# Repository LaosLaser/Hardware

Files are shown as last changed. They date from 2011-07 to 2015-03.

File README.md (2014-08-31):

Hardware
========

PCB Designs for the laos project (mainboard)
* 2 - Development version
* rev0.1 - small first series
* rev0.2 - used in various lasers
* rev0.3 - latest version
* rev0.4 - Nr of fixes. Introduced dagerous hardware errors: Grounds disconnected. See wiki!
* rev0.5 - Hardware fixes: routing and ground plane
* rev0.6 - Hardware fix: microSD card holder pinout fixed

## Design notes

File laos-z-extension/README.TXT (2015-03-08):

This PCB routes STEP and DIRECTION to 4 pololu's at the same time. It is
used to drive 4 stepper motors on a big Z Frame.

Created by Jaap @ Tuxic.nl, 2015. 

This work falls under the CreativeCommons Attribution-ShareAlike license.
http://creativecommons.org/licenses/by-sa/4.0/

Shortcomings in commit 4bb586817d:

* Pin order of P2 is the opposite of the Pin Order of the output on the
  LaOS board. It would be logical to match those.
* P2 should have an extra pin for ENABLE. It should still be possible to
  use the board without connecting this pin.
* INPUT on P2 could be buffered or seperated with opto coupler for better
  reliability

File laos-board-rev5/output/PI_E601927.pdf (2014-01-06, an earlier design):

### E601927 PCB view TOP (topview)

### E601927 TOP layer Image (topview)

E601927 BOTTOM layer Image (topview)

E601927 PCB view BOTTOM (bottomview)

# E601927 PCB Mechanical view (topview)

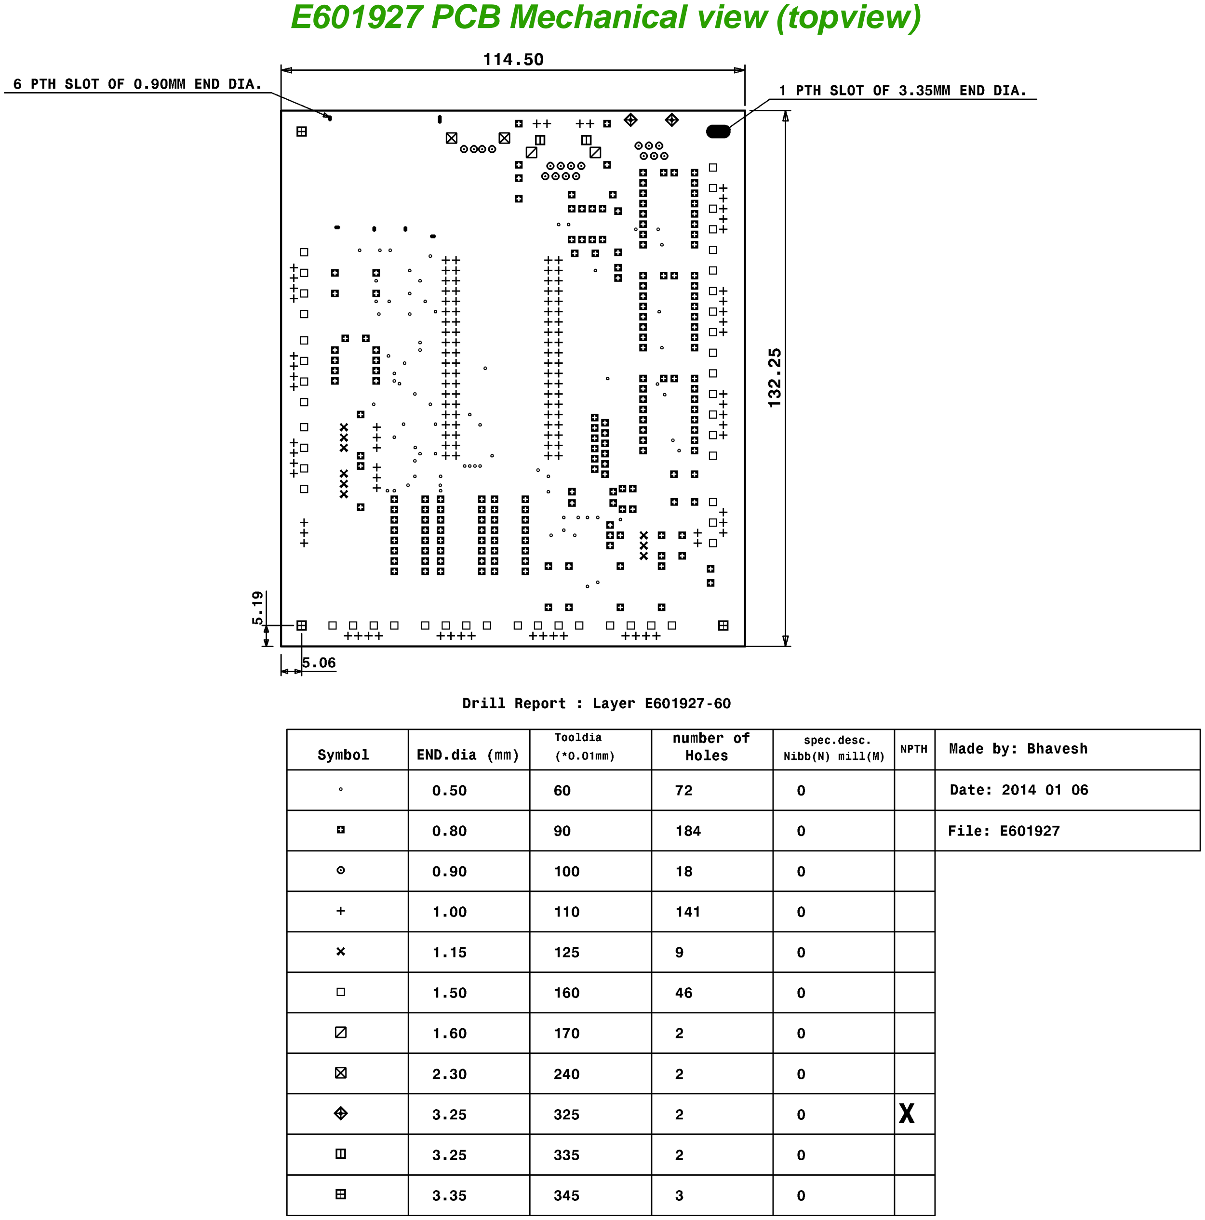
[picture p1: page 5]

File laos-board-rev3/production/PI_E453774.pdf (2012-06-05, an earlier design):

# E453774 PCB view TOP (topview)

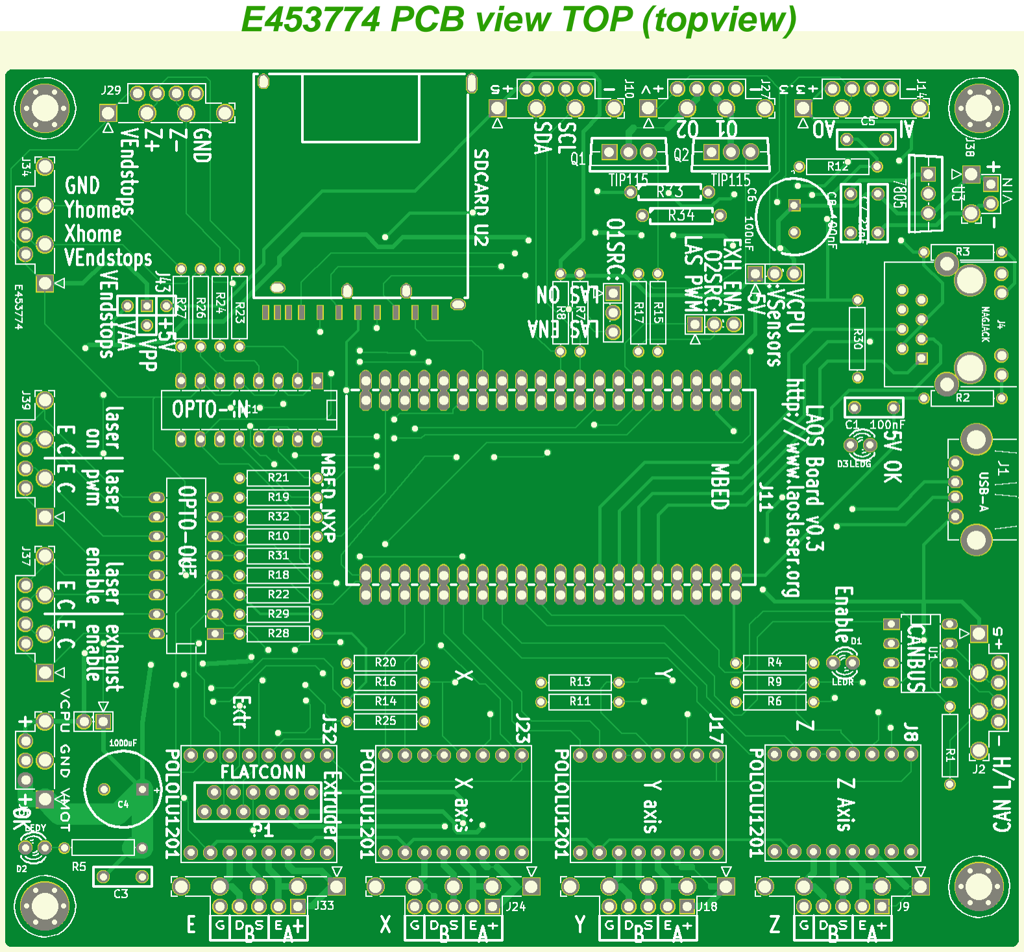
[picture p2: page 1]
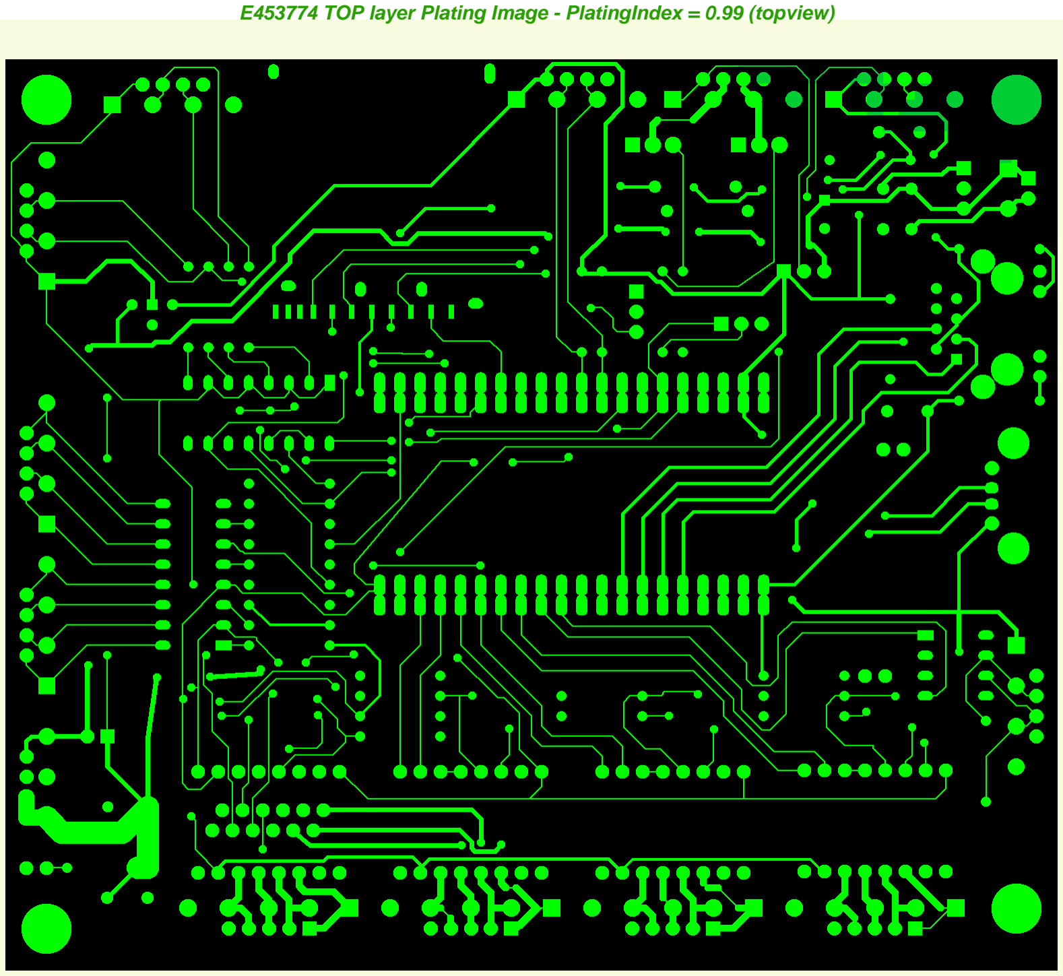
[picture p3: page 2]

E453774 TOP layer Plating Image - PlatingIndex = 0.99 (topview)

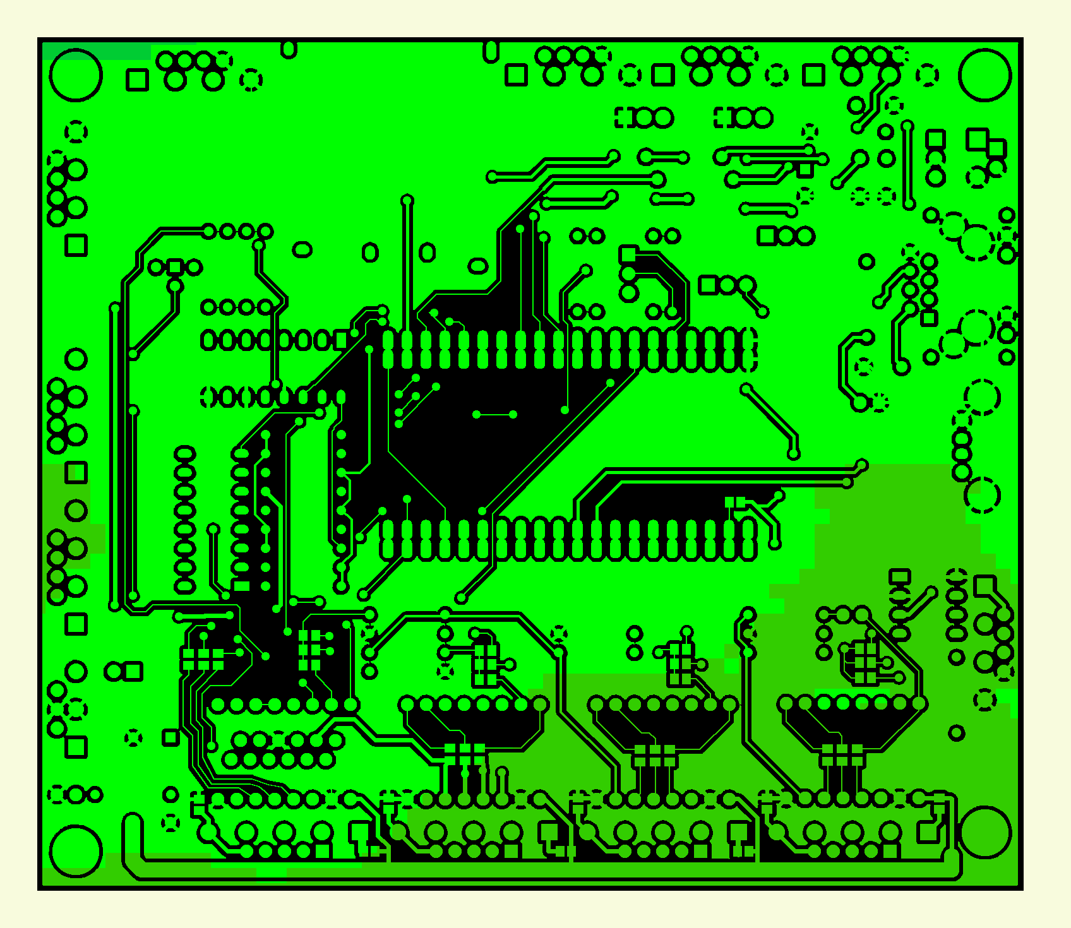
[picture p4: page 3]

E453774 BOTTOM layer Plating Image - PlatingIndex = 0.8 (topview)

## E453774 PCB view BOTTOM (bottomview)

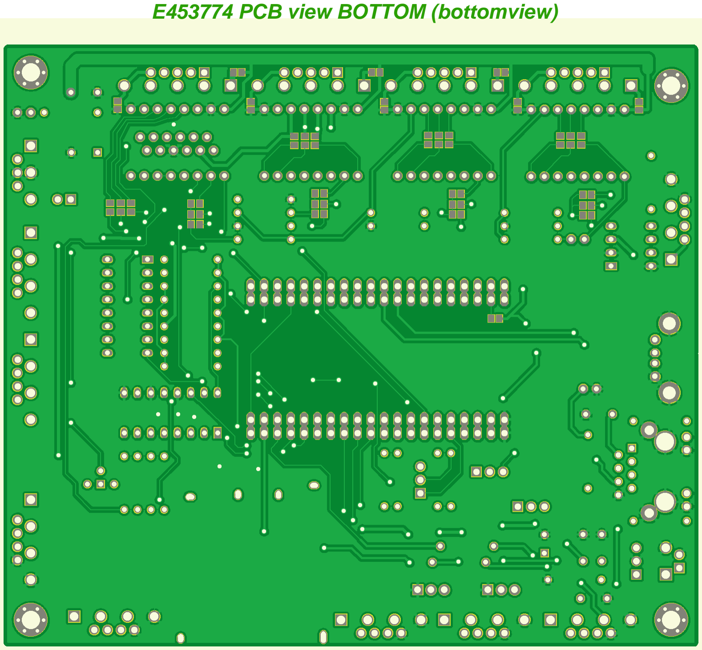
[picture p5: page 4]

# E453774 PCB Mechanical view (topview)

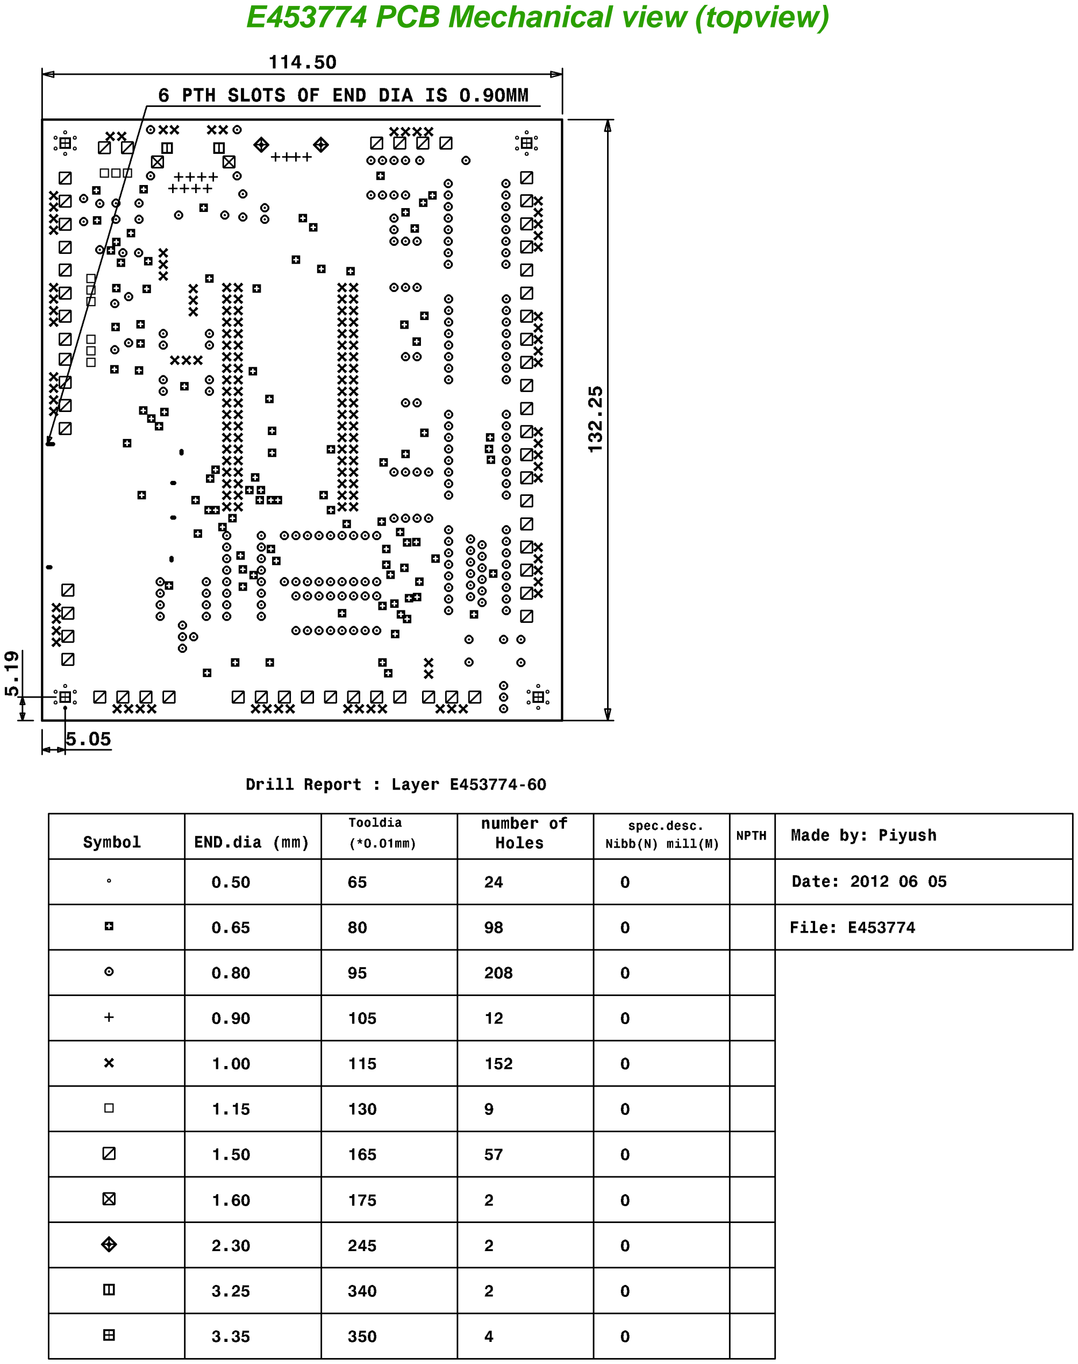
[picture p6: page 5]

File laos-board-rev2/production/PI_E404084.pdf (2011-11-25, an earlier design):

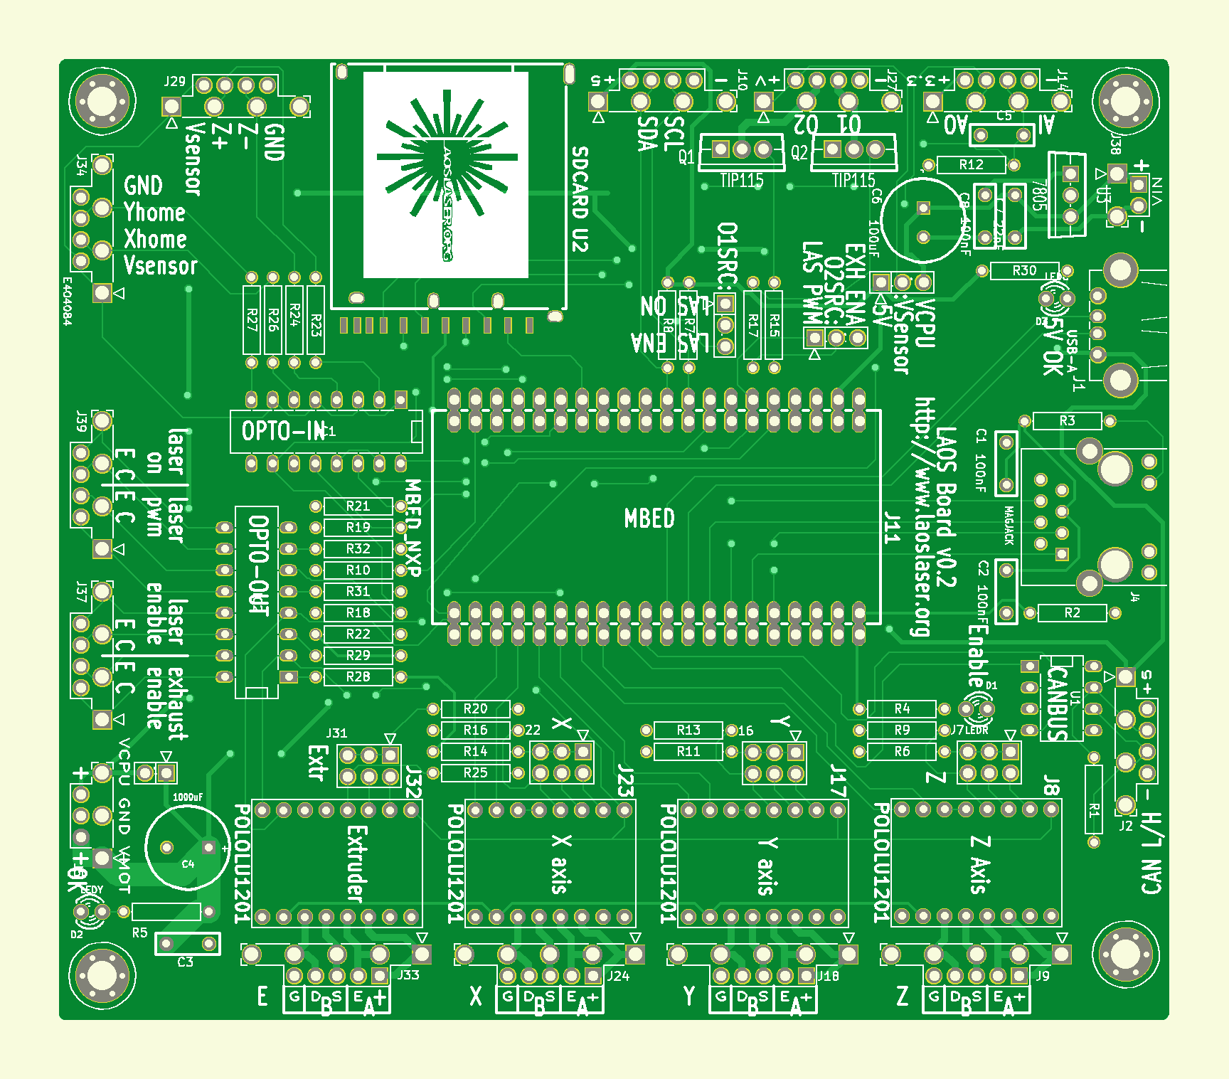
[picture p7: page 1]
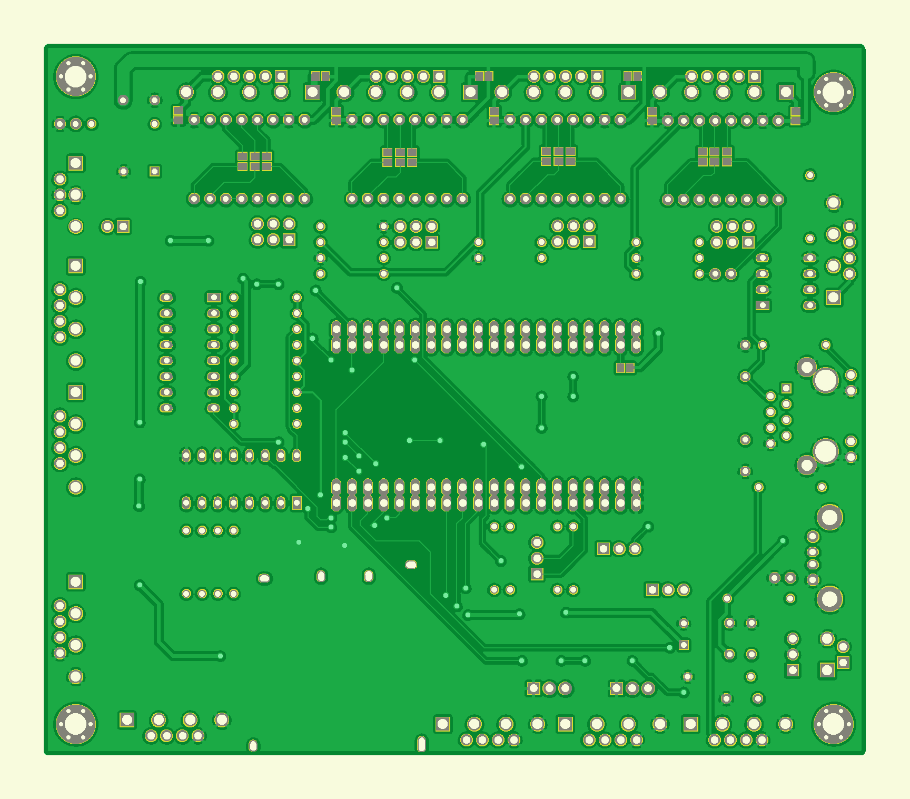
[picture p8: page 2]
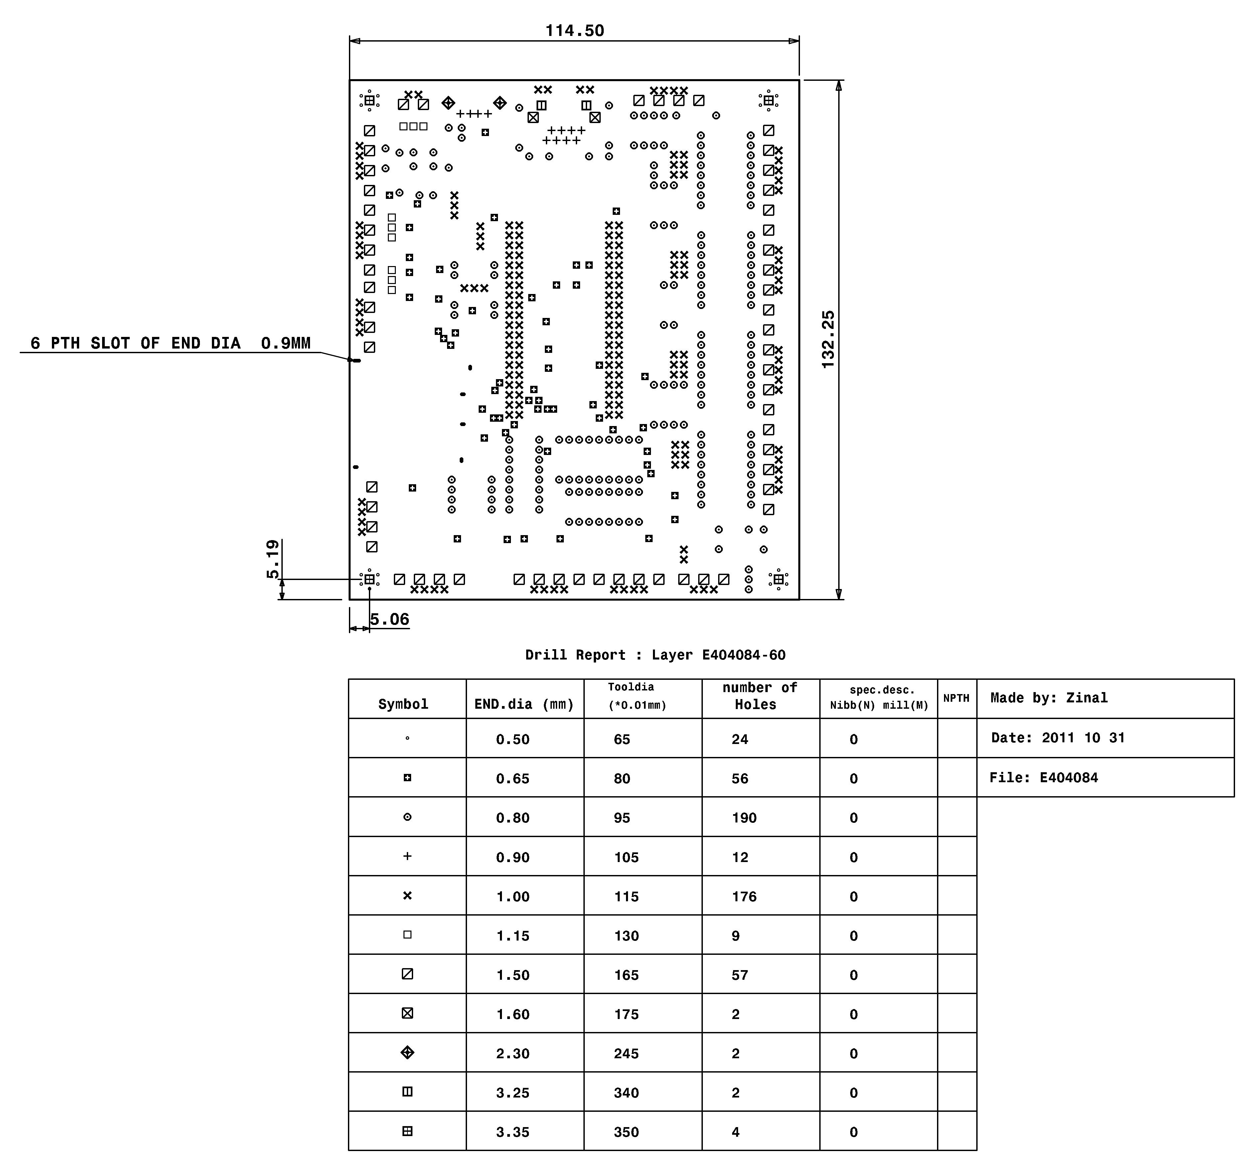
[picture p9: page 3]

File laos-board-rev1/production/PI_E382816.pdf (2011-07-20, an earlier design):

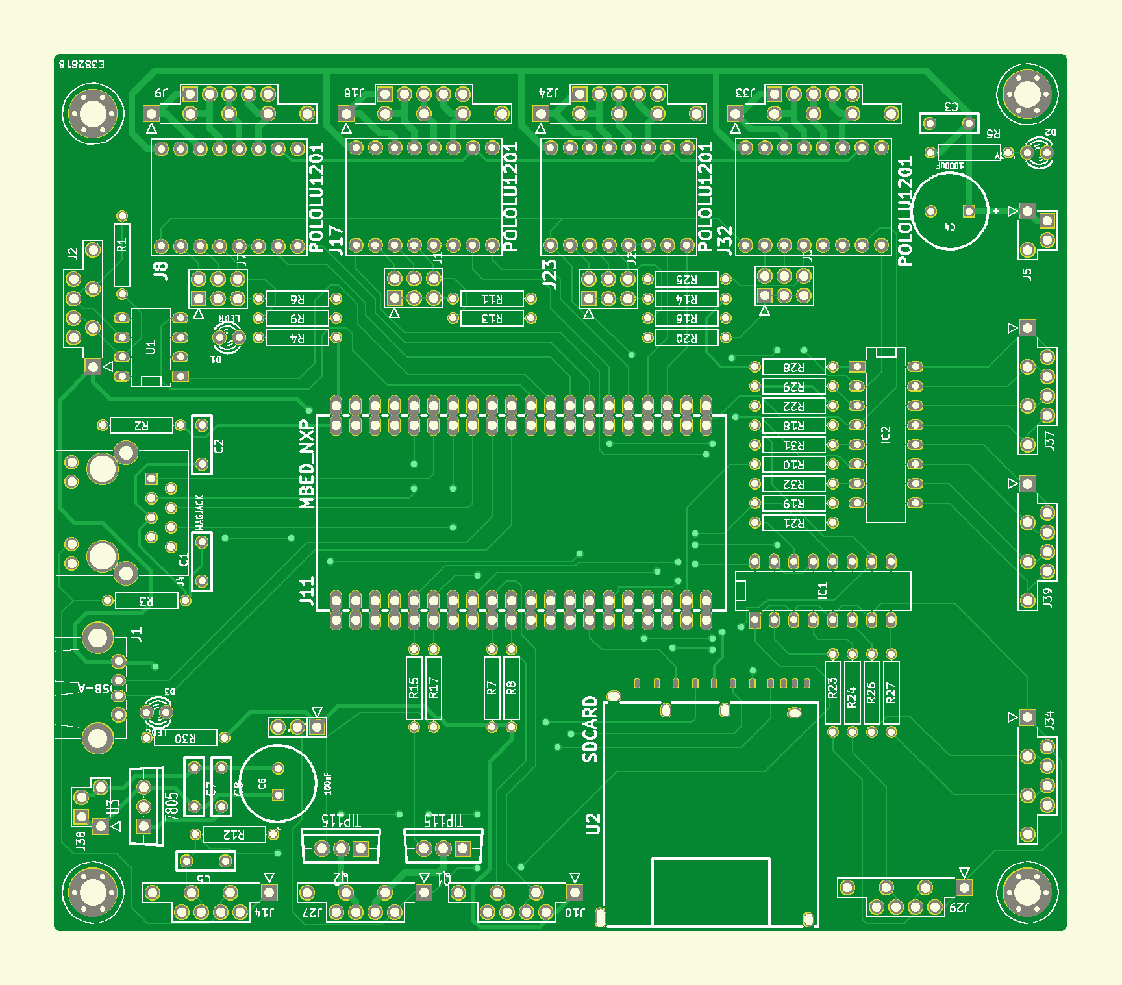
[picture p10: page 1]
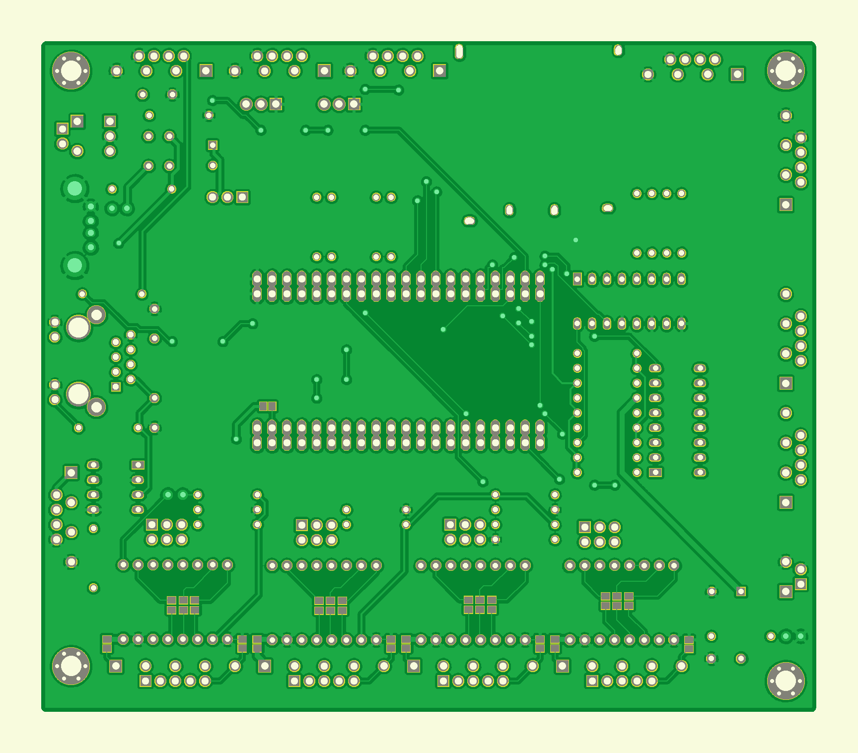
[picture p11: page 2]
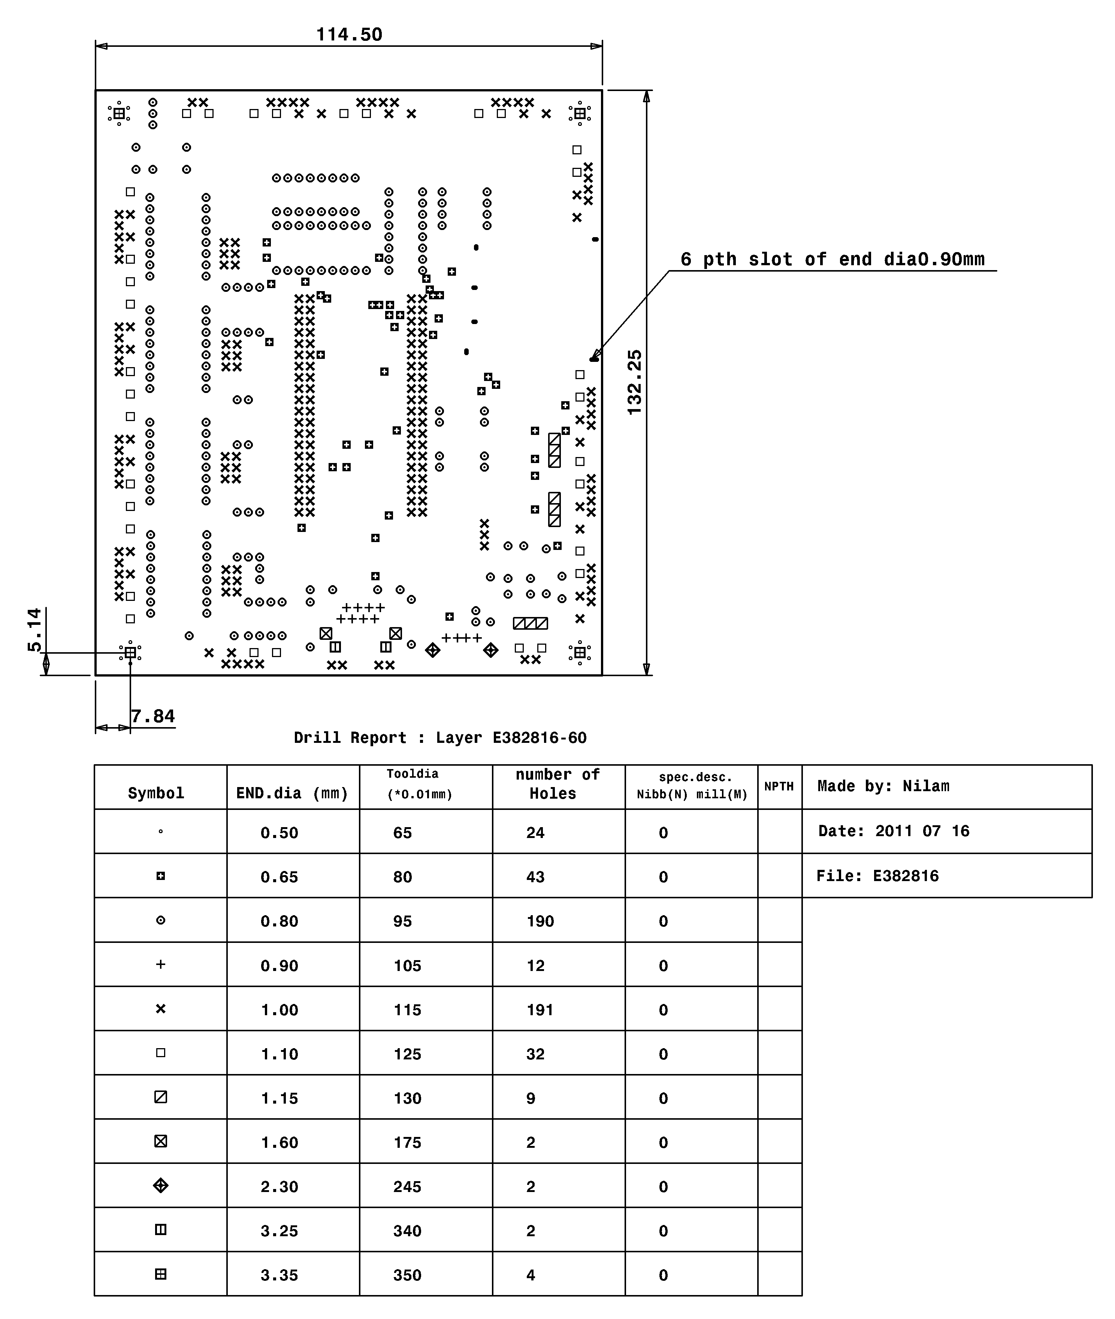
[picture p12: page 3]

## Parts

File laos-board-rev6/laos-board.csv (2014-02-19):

ref | value | footprint | Field1 | Field2 | Field3 | Field4 | Field5 | Field6 | Field7 | Field8
C1 | 100nF | C_CER
C2 | 100nF | C_CER
C3 | 100nF | C_CER
C4 | 1000uF | CCAP_5MM
C5 | 100nF | C_CER
C6 | 100uF | CCAP_3.5MM
C7 | 22nF | C_CER
C8 | 100nF | C_CER
C9 | 100uF | C1V7HF
C10 | 100uF | C1V7HF
C11 | 100uF | C1V7HF
CAN1 | Molex 95501-2641 | RJ12_MOLEX_95501-2641 | Molex | 95501-2641
D1 | LEDR | LED-3MM
D2 | LEDY | LED-3MM
D3 | LEDG | LED-3MM
H1 | MOUNT_HOLE | HOLE_3MM
H2 | MOUNT_HOLE | HOLE_3MM_OVAL
H3 | MOUNT_HOLE | HOLE_3MM
H4 | MOUNT_HOLE | HOLE_3MM
IC1 | KB847 | 16DIP300-ELL | 2001656 | 619-2026
IC2 | KB847 | 16DIP300-ELL
J1 | USB-A | con-usb-USB-A-H
J3 | USBPWR | SJ
J4 | MAGJACK | RJ45_HALO_HFJ11 | MAGJACK | SI-60002-F | 1137981 | 741-8477
J5 | CONN_3 | CONN_3
J7 | JP_3 | SJ_3
J8 | Pololu 1182 (A4988) | POLOLU1201 | Pololu 1182
J9 | ZAXIS | CONN_5
J10 | I2C | CONN_4 | 1234 | 5678
J11 | MBED NXP | MBED | 1761179 | 703-9238
J12 | JP | SJ
J14 | ANALOG | CONN_4
J16 | JP_3 | SJ_3
J17 | Pololu 1182 (A4988) | POLOLU1201 | Pololu 1182
J18 | YAXIS | CONN_5
J19 | JP | SJ
J22 | JP_3 | SJ_3
J23 | Pololu 1182 (A4988) | POLOLU1201 | Pololu 1182
J24 | XAXIS | CONN_5
J25 | JP | SJ
J27 | OUTPUT | CONN_4
J28 | VSENSOR | SIL-3-noarrow
J29 | INPUT12 | CONN_4
J34 | INPUT34 | CONN_4
J37 | OUTPUT12 | CONN_4
J39 | OUTPUT34 | CONN_4
J40 | JP | SIL-2
J41 | O1_SRC | SIL-3-noarrow
J42 | O2_SRC | SIL-3-noarrow
J43 | CONN_4 | SIL-4a
P1 | FLATCONN | FLAT-12
Q1 | TIP110 | TO220V-BCE
Q2 | TIP110 | TO220V-BCE
R1 | 120R | R4
R2 | 1K | R4
R3 | 1K | R4
R4 | 1K | R4
R5 | 1K | R4
R7 | 2K2 | R4
R8 | 2K2 | R4
R10 | 10k | R4
R12 | 1k | R4
R15 | 1k | R4
R17 | 1k | R4
R18 | 10k | R4
R19 | 10k | R4
R21 | 10k | R4
R22 | 10k | R4
R23 | 1K | R4
R24 | 1K | R4
R26 | 1K | R4
R27 | 1K | R4
R28 | 330R | R4
R29 | 330R | R4
R30 | 1k | R4
R31 | 330R | R4
R32 | 330R | R4
R33 | 1K | R4
R34 | 100 | R4
U1 | 65HVD251 | 8DIP300-ELL
U2 | Hirose DM1B-DSF-PEJ(82) or Molex 502774-0891 | HIROSE_DM1B-DSF-PEJ_MOLEX_502774-0891 | Hirose/Molex | DM1B-DSF-PEJ(82)/502774-0891
U3 | 7805 | TO220V-123

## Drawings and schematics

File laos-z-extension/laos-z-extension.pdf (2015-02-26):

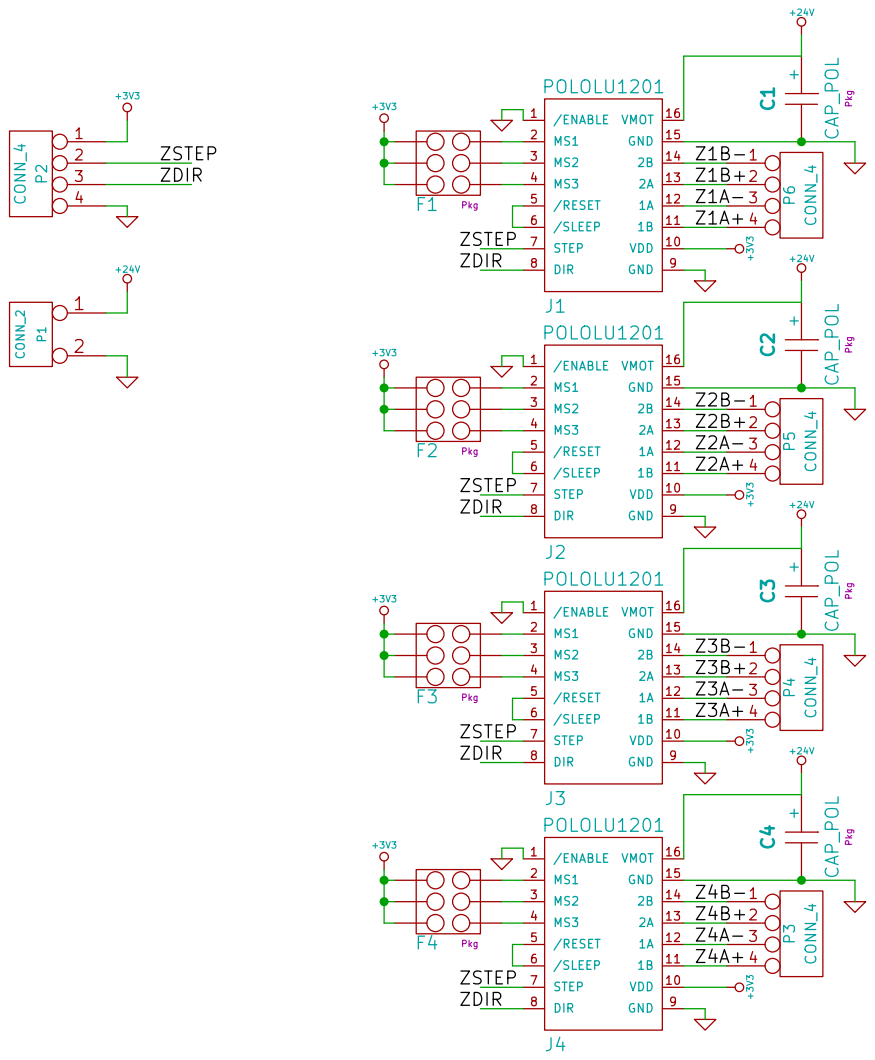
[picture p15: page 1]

Id: 1/1 Title: File: laos-z-extension.sch Sheet: /

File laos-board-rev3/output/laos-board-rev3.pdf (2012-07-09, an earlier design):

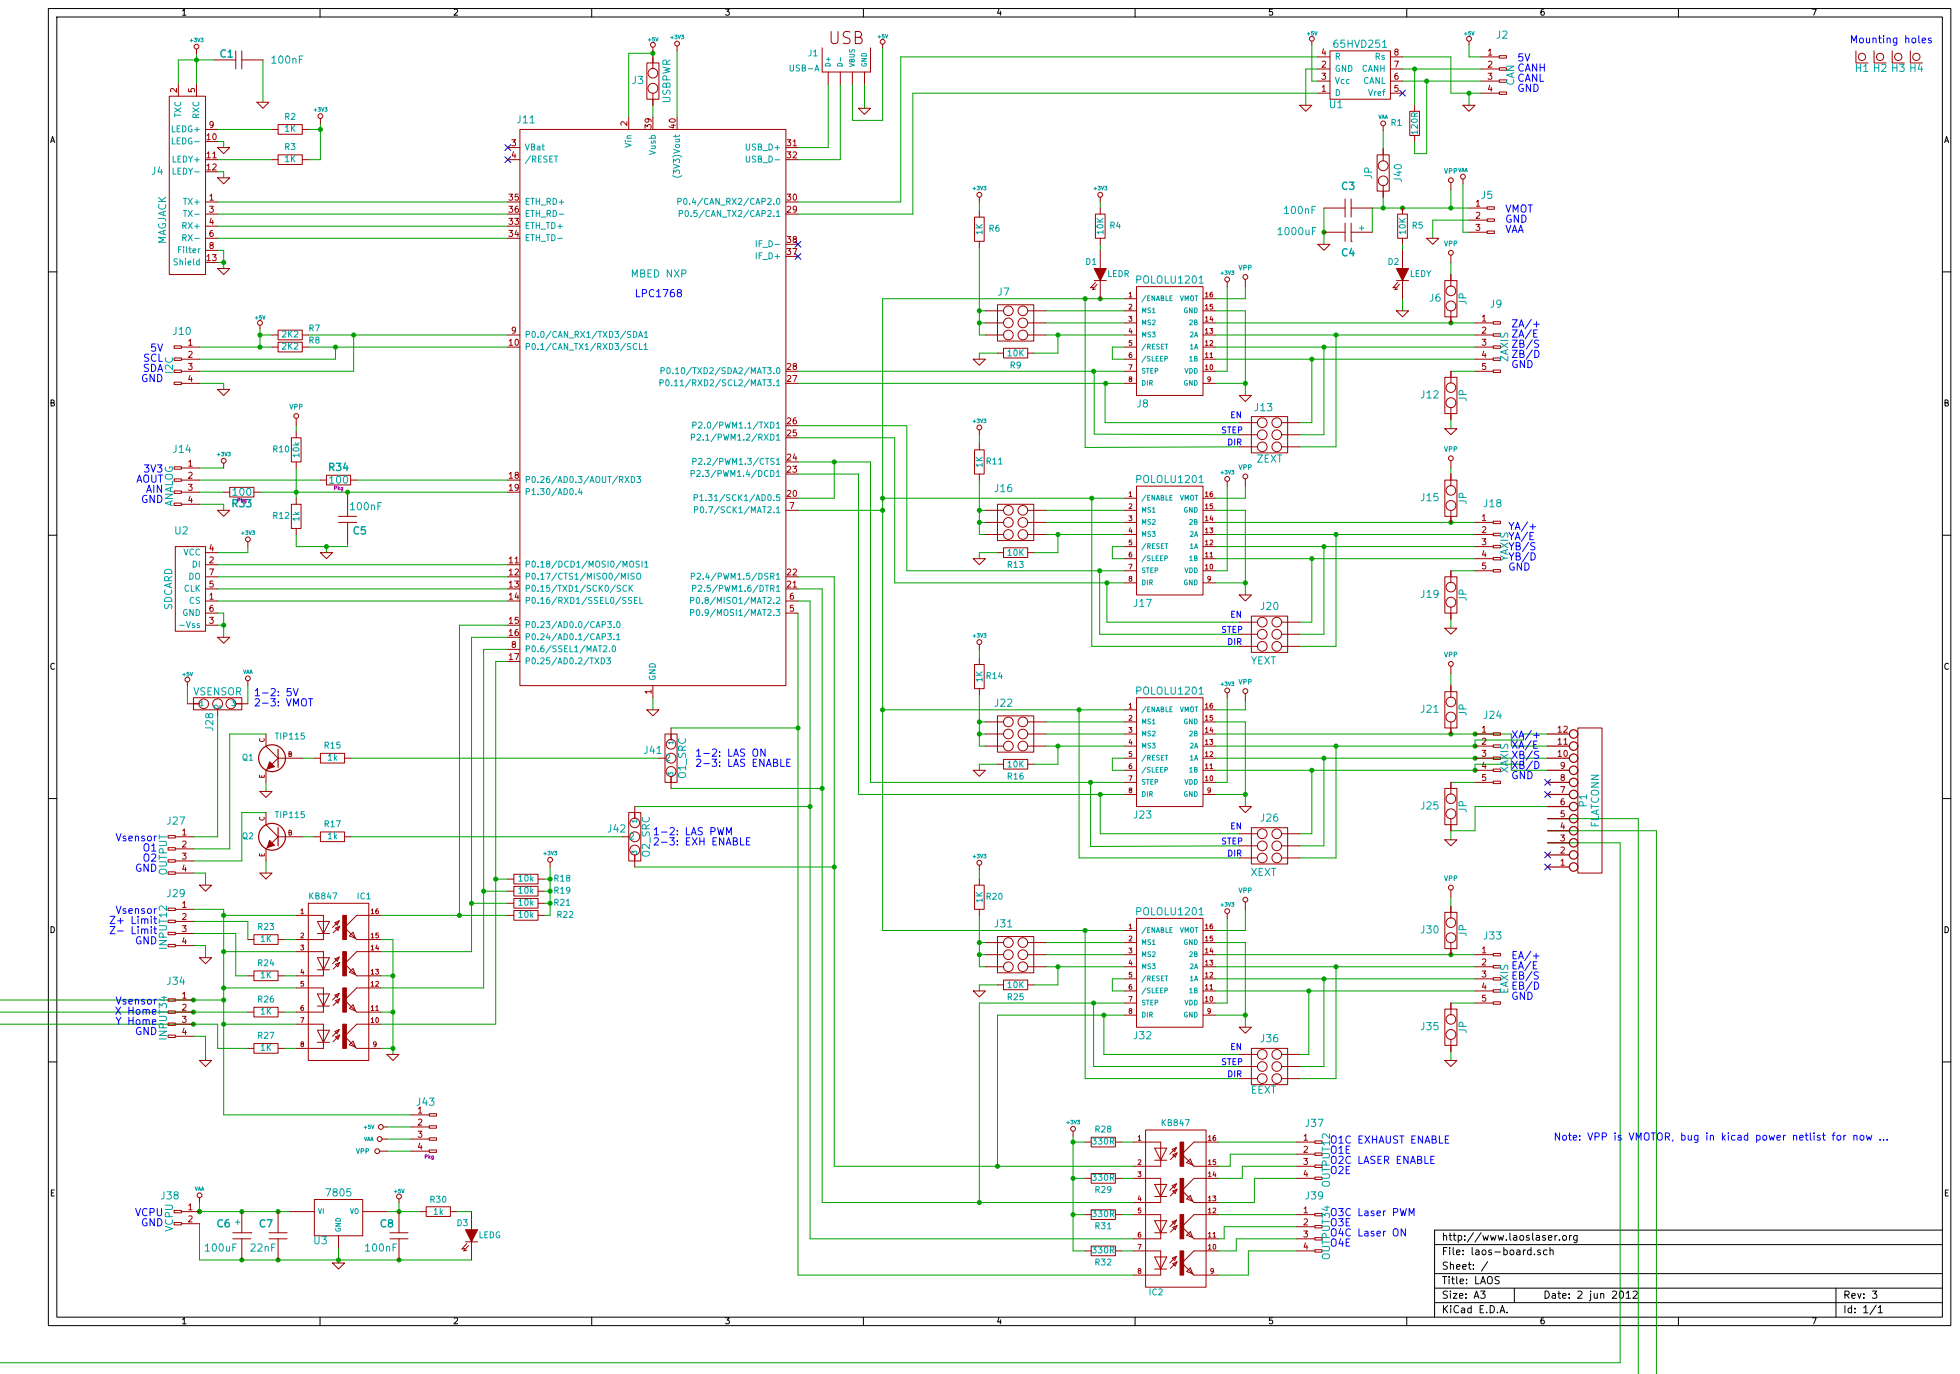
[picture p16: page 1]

Vsensor Z+ Limit Z- Limit GND

Vsensor X Home Y Home GND

Note: VPP is VMOTOR, bug in kicad power netlist for now ...

http://www.laoslaser.org
File: laos-board.sch Sheet: /

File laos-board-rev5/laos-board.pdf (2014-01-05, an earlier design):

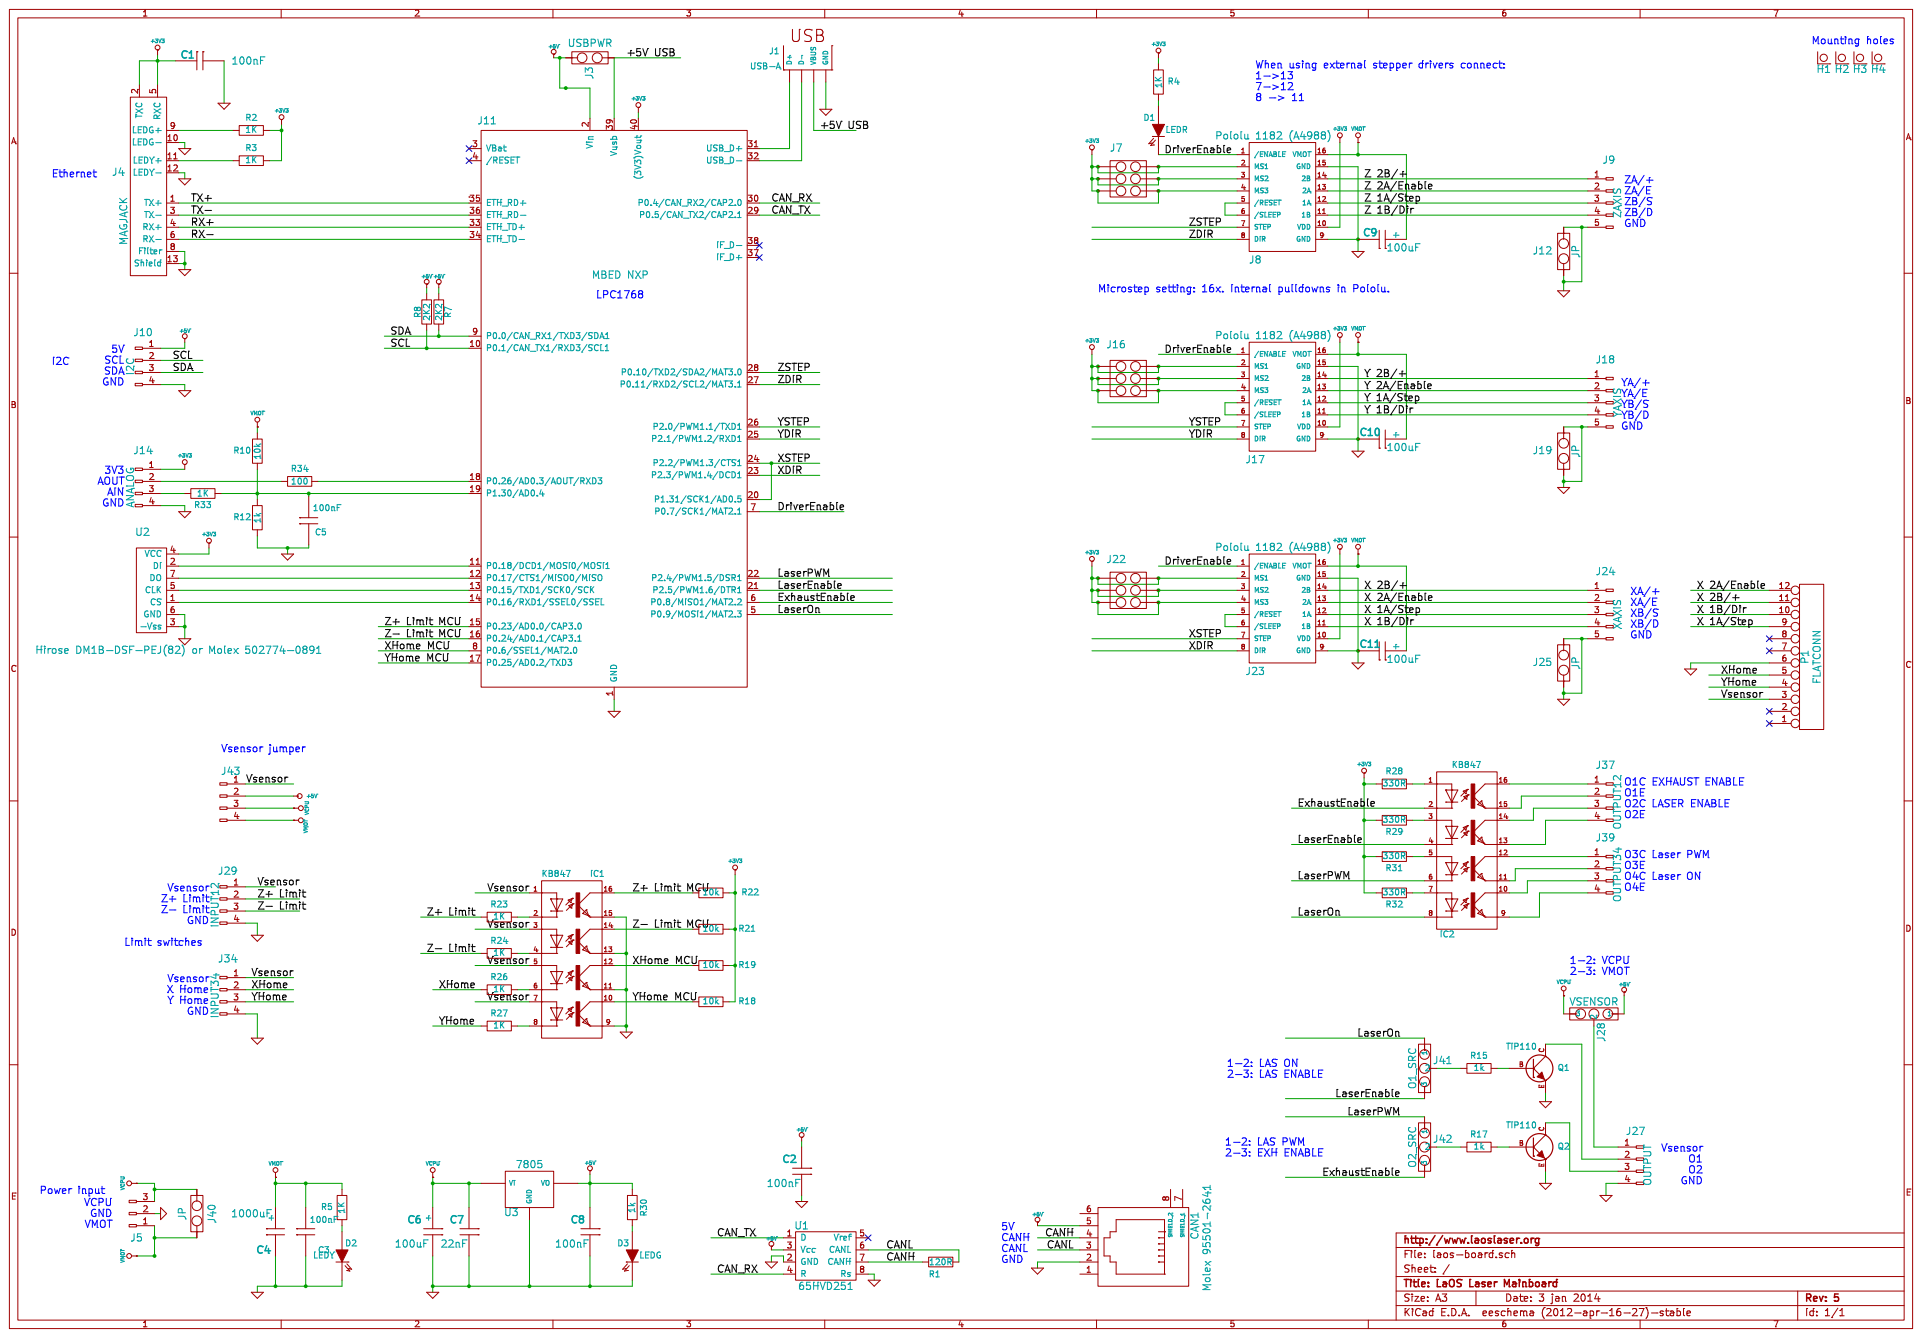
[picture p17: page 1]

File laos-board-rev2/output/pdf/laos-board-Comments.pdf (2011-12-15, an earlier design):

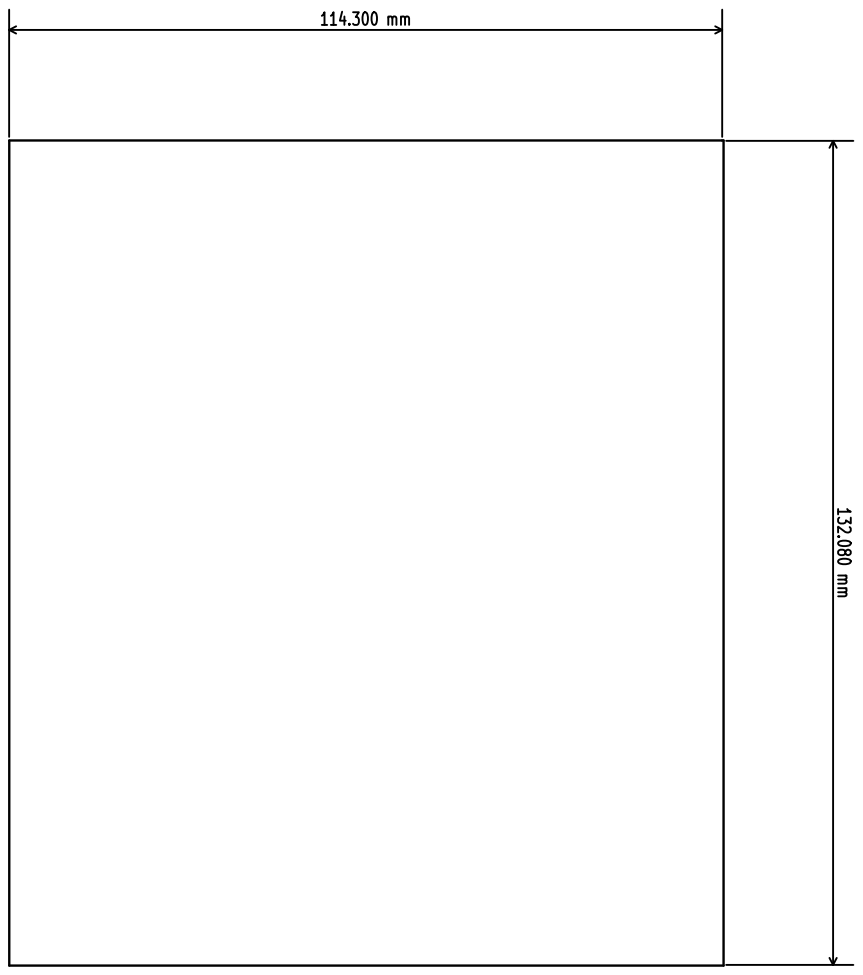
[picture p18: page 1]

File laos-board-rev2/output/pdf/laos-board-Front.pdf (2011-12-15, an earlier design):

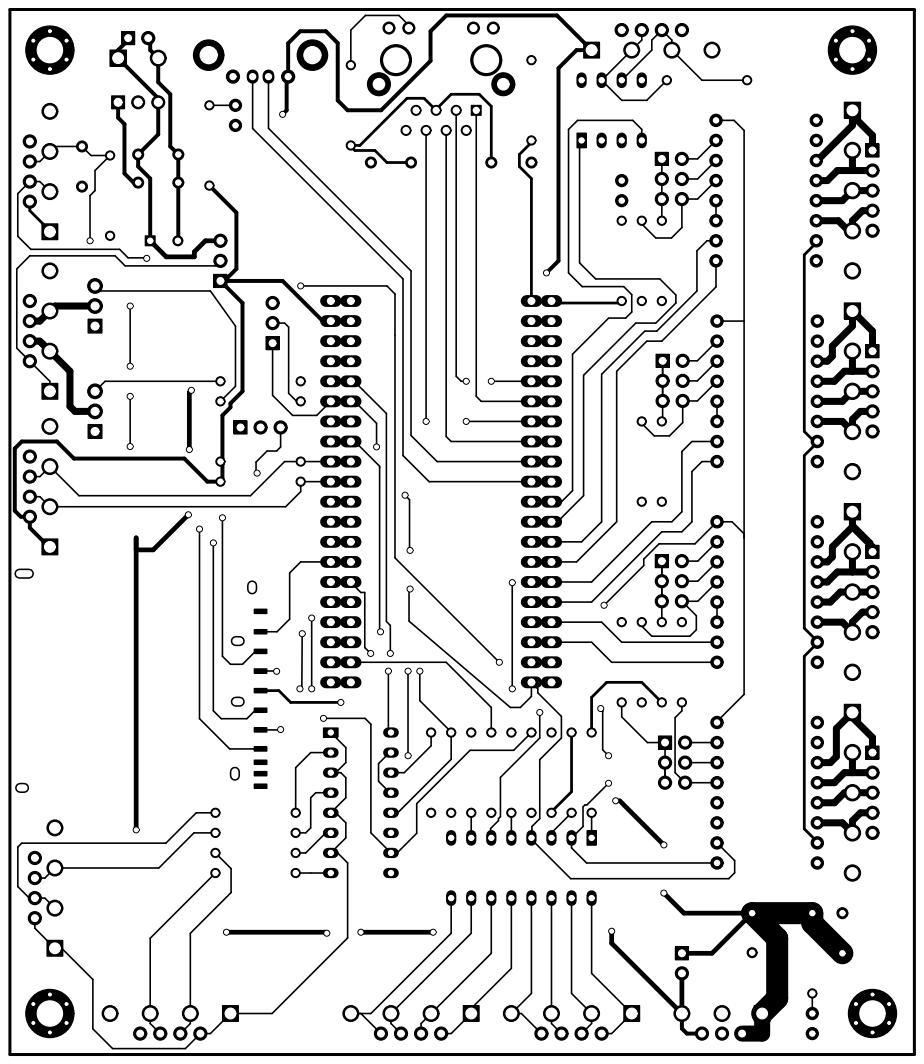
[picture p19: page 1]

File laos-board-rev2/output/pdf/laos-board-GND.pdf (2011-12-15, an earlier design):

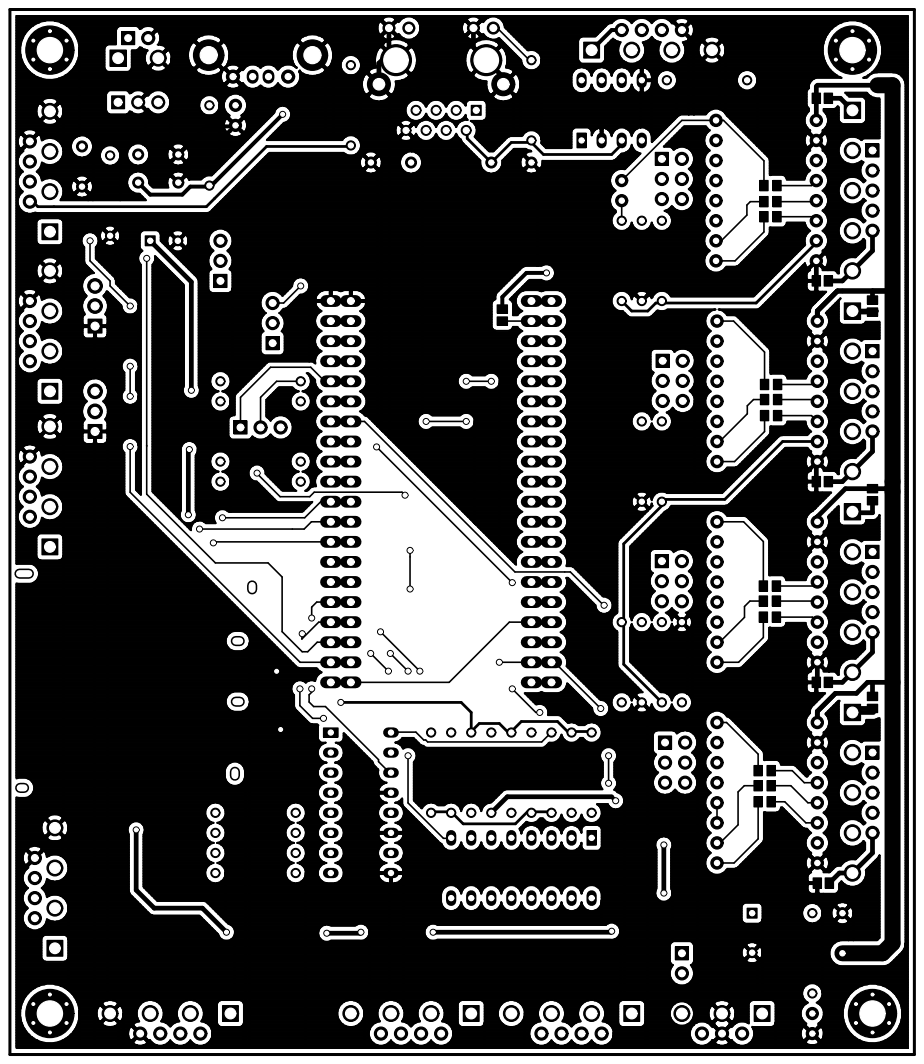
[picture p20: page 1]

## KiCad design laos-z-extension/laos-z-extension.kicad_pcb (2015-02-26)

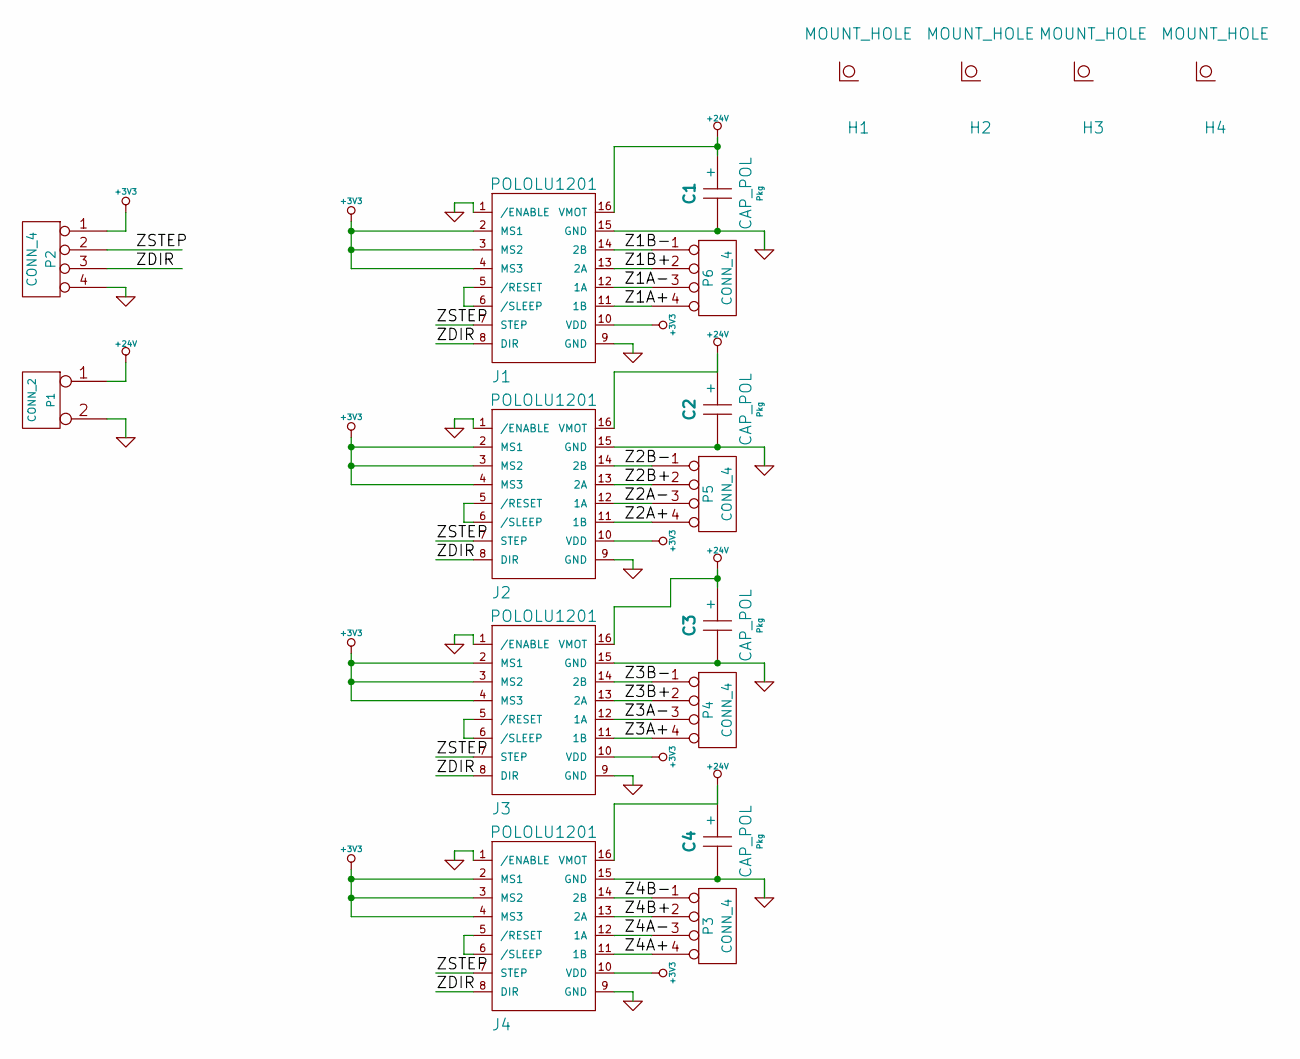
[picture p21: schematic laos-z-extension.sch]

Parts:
C1, C2, C3, C4: CAP_POL; Pkg
H1, H2, H3, H4: MOUNT_HOLE
J1, J2, J3, J4: POLOLU1201
P1: CONN_2
P2, P3, P4, P5, P6: CONN_4

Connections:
+3V3: J1.2 (MS1), J1.3 (MS2), J1.4 (MS3), J1.10 (VDD), J2.2 (MS1), J2.3 (MS2), J2.4 (MS3), J2.10 (VDD), J3.2 (MS1), J3.3 (MS2), J3.4 (MS3), J3.10 (VDD), J4.2 (MS1), J4.3 (MS2), J4.4 (MS3), J4.10 (VDD), P2.1
+24V: C1.1 (+), C2.1 (+), C3.1 (+), C4.1 (+), J1.16 (VMOT), J2.16 (VMOT), J3.16 (VMOT), J4.16 (VMOT), P1.1
/Z1A+: J1.11 (1B), P6.4
/Z1A-: J1.12 (1A), P6.3
/Z1B+: J1.13 (2A), P6.2
/Z1B-: J1.14 (2B), P6.1
/Z2A+: J2.11 (1B), P5.4
/Z2A-: J2.12 (1A), P5.3
/Z2B+: J2.13 (2A), P5.2
/Z2B-: J2.14 (2B), P5.1
/Z3A+: J3.11 (1B), P4.4
/Z3A-: J3.12 (1A), P4.3
/Z3B+: J3.13 (2A), P4.2
/Z3B-: J3.14 (2B), P4.1
/Z4A+: J4.11 (1B), P3.4
/Z4A-: J4.12 (1A), P3.3
/Z4B+: J4.13 (2A), P3.2
/Z4B-: J4.14 (2B), P3.1
/ZDIR: J1.8 (DIR), J2.8 (DIR), J3.8 (DIR), J4.8 (DIR), P2.3
/ZSTEP: J1.7 (STEP), J2.7 (STEP), J3.7 (STEP), J4.7 (STEP), P2.2
GND: C1.2, C2.2, C3.2, C4.2, J1.1 (/ENABLE), J1.9 (GND), J1.15 (GND), J2.1 (/ENABLE), J2.9 (GND), J2.15 (GND), J3.1 (/ENABLE), J3.9 (GND), J3.15 (GND), J4.1 (/ENABLE), J4.9 (GND), J4.15 (GND), P1.2 (PM), P2.4
unnamed: J4.5 (/RESET), J4.6 (/SLEEP)
unnamed: J3.5 (/RESET), J3.6 (/SLEEP)
unnamed: J1.5 (/RESET), J1.6 (/SLEEP)
unnamed: J2.5 (/RESET), J2.6 (/SLEEP)

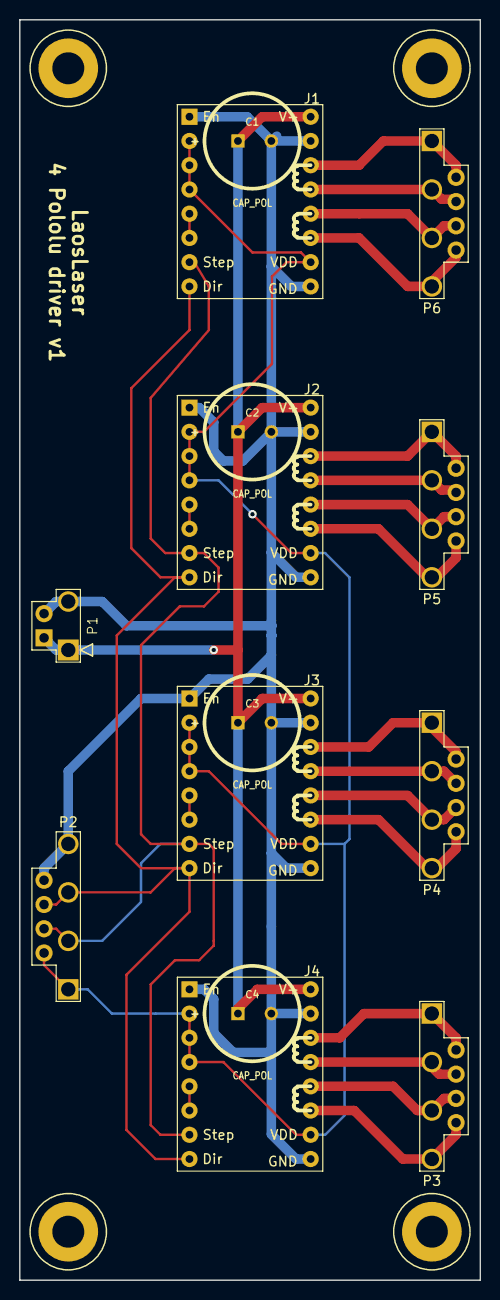
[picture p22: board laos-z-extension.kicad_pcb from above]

Board: 2 copper layers, 48.3 x 132.1 mm, 18 parts (0 on the bottom side), 25 nets.

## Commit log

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2011-03-08 Added rev1 of the board
    [laos-board.sch, pinlist.ods]
2011-03-10 more dataheets, rev2 of board design
    [driver.sch, laos-board.brd, laos-board.sch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]
2011-04-04 Siert's board (after modifications by Peter)
    [MBED LAOS Circuit Board 0.01.brd, MBED LAOS Circuit Board 0.01.sch]
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2011-06-02 simplified schematics Added info on board layout and connector placement
    [laos-board.brd, laos-board.sch]
2011-06-30 Add laos-board revision 2 schematics
    [laos-board.brd, laos-board.sch, mainboard.brd]
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2011-07-01 Add new polulu and some power nets
    [laos-board.sch]
2011-07-01 Laos board 2 schematic completed before check
    [laos-board.sch]
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2011-07-01 Updates before pcb design
    [laos-board.sch]
2011-07-01 Last minute schematic changes
    [laos-board.sch]
2011-07-02 Initial work on laos-board footprints
    [laos-board.brd, laos-board.sch]
2011-07-06 Initial work on module placement
    [laos-board.brd, laos-board.sch]
2011-07-07 More work on module placement for laos-board-2
    [laos-board.brd, laos-board.sch]
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2011-07-12 Wiring to the mbed
    [laos-board.brd, laos-board.sch]
2011-07-12 Wiring one 4 layers
    [laos-board.brd, laos-board.sch]
2011-07-13 More routing work on laos-board-2
    [laos-board.brd]
2011-07-13 More routing before module compacting
    [laos-board.brd]
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2011-07-14 Finish 2 layer routing
    [laos-board.brd, laos-board.sch]
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2011-07-14 Final outputs for review laos-board-2
    [laos-board-Comments.gbr, laos-board-Front.gtl, laos-board-GND.gbl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]
2011-07-14 Add pdf files from postscripts
    [laos-board.brd]
2011-07-15 Change jumpers near polulus
    [laos-board.brd, laos-board.sch]
2011-07-15 Add production files for laos-board v0.1
    [laos-board-Comments.gbr, laos-board-Front.gtl, laos-board-GND.gbl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]
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2011-09-20 schematic updates to work toward rev.2
    [laos-board.sch]
2011-09-20 nog een paar wijzigingen van het schema
    [laos-board.sch]
2011-09-20 Added ethernet PCB modification info for HALO plugs
    [MBED LAOS Circuit Board.brd, MBED LAOS Circuit Board.sch]
2011-09-21 Copied the first production-version of the board to a seperate directory. Do not change anythin in laos-board-rev1, as it will never be used again!
    [laos-board-Comments.gbr, laos-board-Front.gtl, laos-board-GND.gbl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]
2011-09-21 some more rev2 changes
    [laos-board.sch]
2011-10-15 - Checked schematic - Added connector values and pin text - made pin selection for transistor outputs - Made pull-up resistor values 1K.
    [laos-board.sch]
2011-10-16 Connect forgotten nets and generate new netlist
    [laos-board.sch]
2011-10-16 Import new netlist into pcb
    [laos-board.brd]
2011-10-16 Connect some new nets in the pcb, bad ubuntu
    [laos-board.brd]
2011-10-16 Connect some new nets in the pcb, and some modules, bad ubuntu
    [laos-board.brd, laos-board.sch]
2011-10-16 some more updates to the phoenix connectors
    [laos-board.brd]
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2011-10-17 connected pin 21 mbed to J41
    [laos-board.brd]
2011-10-27 Exchange VMOT for VPP because of weird kicad bug
    [laos-board.brd, laos-board.sch]
2011-10-27 updated former VMOT net into VPP
    [laos-board.brd]
2011-10-27 moved text to right places and added comments
    [laos-board.brd]
2011-10-27 added some more gnd, +5v etc
    [laos-board.brd]
2011-10-30 Added more text to connectors. Some problems still exist with Vaa / Vpp nets (not connected). and Vin(-) is not connected to GND
    [laos-board.brd]
2011-10-30 changes after Peter had a look at the board
    [laos-board.brd, laos-board.sch]
2011-10-30 connector j5 with 3 wires
    [laos-board.brd, laos-board.sch]
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2011-10-31 modified pin3 diameter of CONN_3 from 1 to 1.5mm added extra text for jumpers changed track width for Vmot Changed connector orientation Added logo
    [laos-board.brd, laos-board.sch]
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2011-12-15 Removed all outdated output files (Gerbers, PS and PDF) Still need to add new ones, and production files used to order the V2 PCB's
    [laos-board-Comments.gbr, laos-board-Front.gtl, laos-board-GND.gbl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]
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2012-01-10 svg files for schematic, static rev dir
    [laos-board-Comments.gbr, laos-board-Front.gtl, laos-board-GND.gbl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]
2012-05-30 new board order (rev0.3) coming up
    [laos-board.brd, laos-board.sch]
2012-05-30 forgot to update version number of the schema!
    [laos-board.sch]
2012-06-02 changes made in Arnhem, ready to go?
    [laos-board.brd, laos-board.sch]
2012-06-02 updated J43 to a 3-direction jumper
    [laos-board.brd]
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2012-06-02 renamed pins of flatcable conform official order
    [laos-board.brd, laos-board.sch]
2012-06-03 version with swapped usb/network
    [laos-board.brd, laos-board.sch, laos-board2.brd]
2012-06-03 cleanup and added texts
    [laos-board2.brd]
2012-06-03 added swap of network/usb to main
    [laos-board.brd, laos-board2.brd]
2012-06-03 as ordered dd 2012-06-03
    [laos-board-Comments.gbr, laos-board-Front.gtl, laos-board-GND.gbl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]
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2012-06-13 corrected location of pdf files for board rev0.2
2012-09-30 first commit for rev4
    [laos-board.brd, laos-board.sch]
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2012-09-30 added RJ12 for CAN
    [laos-board.brd, laos-board.sch]
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2012-10-02 replaced 3v3 voltage regulator, added capacitors for Pololu decoupling
    [laos-board.brd, laos-board.sch]
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2013-10-27 Started with new revision, cleaned up the schematic and checked schematic against the old pcb to make sure I didn't break anything
    [laos-board-Comments.gbr, laos-board-Front.gtl, laos-board-GND.gbl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]
2013-11-10 E-axis removed, pololu default 16x microstepping. Fixes #6
    [laos-board.sch]
2013-11-10 'Pololu' means Pololu's A4988 drivers, not the DRV882x drivers. Fixes #6
    [laos-board.sch]
2013-12-23 First functional version, TODO: some polishing and refining
    [laos-board.brd, laos-board.sch]
2013-12-23 Resized texts, nice spacing for certain traces, cleaned up track widths
    [laos-board.brd]
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2014-01-03 Sikscreen texts on back side, output files generated
    [laos-board-Back.gbl, laos-board-Comments.gbr, laos-board-Front.gtl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]
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2014-02-19 Fixed O1 and O2 texts, Enlarged holes of J43, clarified text for J43
    [laos-board.brd]
2014-02-19 Copied connector information to bottom for J5, J9, J18, J24; corrected connector spacing for J10, J14, J27; moved C6
    [laos-board.brd, laos-board.csv]
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2014-08-31 MicroSD card holder pinout fixed. Issue from forum, see http://redmine.laoslaser.org/boards/1/topics/689?r=729#message-729 for more information
    [laos-board-Back.gbl, laos-board-Front.gtl, laos-board-Mask_Back.gbs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]
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
